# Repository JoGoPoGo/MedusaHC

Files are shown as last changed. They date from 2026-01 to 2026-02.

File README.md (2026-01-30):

# MedusaHC (Beta)

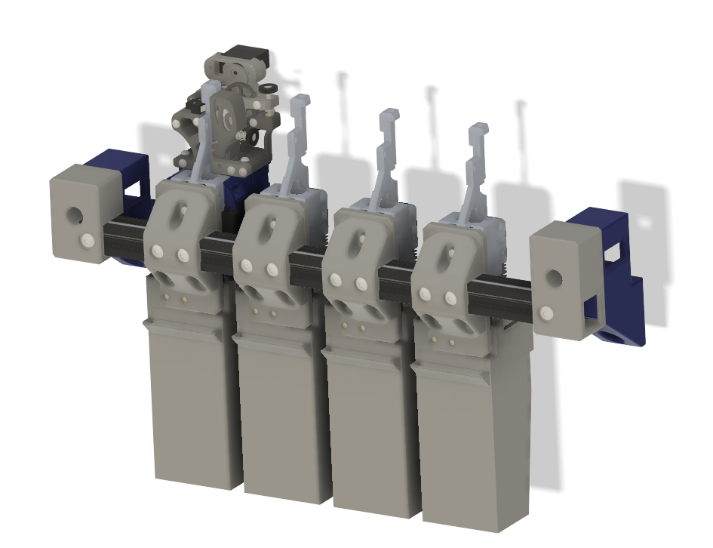
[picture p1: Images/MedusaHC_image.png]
MedusaHC


MedusaHC is an open-source toolchanger (hotend-changer) project.  
This is a beta version of the project. It is not finished yet, and there may be bugs during operation. The project will be updated gradually.

The project is fully open. You can do whatever you want with it.  
Only one request: it is not required, but I would be very grateful if you mention me in your modifications and derivatives of this project.

## Support the project

If you have the ability and desire to support the project, you can do it in several ways:

- Patreon — monthly support: https://patreon.com/Irbis3D  
- Ko-fi / Buy Me a Coffee — one-time donations: https://buymeacoffee.com/Irbis3D  
- YouTube Super Thanks — under any video: https://youtube.com/@Irbis3D  

Your support helps me create more content, upgrade gear, and keep experimenting with cool ideas.

Also, by buying parts using my links, you help as well.

## Credits

This project uses some work and ideas from the Dragonburner project by chirpy2605:  
https://github.com/chirpy2605/voron/tree/main/V0/Dragon_Burner

As well as from Sherpa_mini-Extruder by Annex-Engineering  
https://github.com/Annex-Engineering/Sherpa_Mini-Extruder

## Current status and compatibility

Right now, MedusaHC is an add-on for my Duender project:  
https://www.printables.com/model/1300968-duender-mgn9h-2x-creality-ender-3-corexy-convertio

Potentially, the project can be adapted for other classic CoreXY printers (as long as the printer has enough space in the front for the hotends and the bases). Theoretically, with small modifications, MedusaHC can also be adapted for CoreXY with a flying gantry.

The point of the project is that, unlike classic toolchangers, MedusaHC swaps only the hotend as a tool (with heater, thermistor, and fan). I am not the first who did this and I will not be the last. This topic is actively discussed and developed on my  
Discord server - https://discord.gg/ae44FHv786

## Documentation and audience

At the moment, the project does not have a full detailed assembly manual and is intended for experienced users.

Later I will make a full video where I explain how everything works and how to set it up. There is also a chance that, thanks to subscribers, after some time there will be a normal text manual with pictures.

For a general understanding, I recommend watching the first video about this project on my YouTube channel. You will not find all the information there, but you can get a general idea of how it works.

MedusaHC video (https://www.youtube.com/watch?v=hpV5Z1TnGdY)

## Parts, BOM, and files

Link to BOM

https://docs.google.com/spreadsheets/d/1xkOzb10DBJzalW4n1tYroh-m_ZFsTQipC1BpUh5ZMWY/edit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

For this project you need to buy quite a lot of parts. I tried not to use expensive and rare components. The list of all required parts can be found in the file MedusaHC_BOM.txt. This file will be updated as the project updates.

You can also find and export the print models yourself from the STEP file (the file was created in Fusion360. There were issues when opening it in FreeCAD, possibly due to some format mismatch).

There are also all STL files. In addition, you can use the 3MF file. This is an exported OrcaSlicer project, where you can see the orientation of all parts, the marked areas where supports are needed, and the settings I used to print the parts. This file will be useful later during setup, because it contains a full slicer config for MedusaHC.

To understand how everything should be assembled, for now use the STEP file. I printed all parts in ABS with 98% infill.

## Important notes

All parts must be printed with good enough quality so that parts do not get stuck inside each other. Some contact surfaces may need a bit of sanding to make them smooth.

When installing magnets (I glued them, and all magnet holes have access from the back for removing magnets), be careful and do not mix up the polarity.

The M3 pins that act as hotend guide pins must be pressed into the plastic as straight as possible. I hammered them in, but it is better to do it carefully using a vise. The two lower M3 30mm pins are mandatory. The upper M3 20mm pins are optional, if the hotend does not hold firmly enough.

On the hotend, the matching holes for the pins must be prepared. Personally, I used M3 inserts for this, and I drilled them first with a 3mm bit (they are usually about 2.9mm), and then with a 3.2mm bit (my bits are closer to 3.1mm). Even though the size looks odd, these drill bits are quite common.

Before drilling the actual part, I recommend testing on some test piece to make sure the hole is not too large. The pins must slide in freely, but must not be loose.

Maybe later it will be possible to use brass bushings of the correct diameter, but they take more space and may not fit.

The pressure lever spring for the feeder from the standard Sherpa Mini kit does not fit. I just found a suitable spring in my spare parts. When a spring with known dimensions is selected, I will add this information to the BOM.

The spring for the feeder opener lever is just a regular spring from a ballpoint pen.

Other than that, you just need to assemble everything carefully so nothing is loose and nothing binds. As I said earlier, I will explain more nuances in the video.

## Electronics

For this project, I use the **BTT Manta M8P** board. For a 4-hotend configuration, it can be considered the most optimal option. It has enough ports for absolutely everything, including 4 hotend heaters and even a dedicated Servo port (which is sufficient without a DC-DC converter). My configuration files are set up specifically for this board with a **CB2** module.  
https://s.click.aliexpress.com/e/_oktZaKt

Roughly the same capabilities are provided by boards like **BTT Octopus Pro**, **Kraken**, and other “large” boards, with the main difference being that the HOST is located separately.  
https://s.click.aliexpress.com/e/_c2wuASWJ  
https://s.click.aliexpress.com/e/_c3kPDyx1

When using other boards, it is possible to connect additional boards to a single host.

### Ports required per hotend (on the controller board)

For each hotend, the board must have the following ports:

- heater port (MOSFET-controlled; can be used either hotend heaters or the bed)  
- thermistor port  
- fan port (either PWM-controlled or a constant 24V port)  
- endstop port for the endstop located on the base of that hotend  

### Ports required for the toolhead

- one extruder motor port  
- part cooling fan port(s)  
- toolhead endstop port  
- port for the auto-calibration sensor (I use **BTT Eddy** connected via CAN)  
- servo port — if the board does not have a dedicated servo port capable of supplying stable 5V under load, it is recommended to power the servo via a **24V→5V DC-DC converter** from the main power supply  

### Power considerations

Additional hotends require additional power from the PSU.

From experience, a standard **350W** power supply is reliably sufficient for **2 hotends**.  
For **3 hotends**, it can be enough with a high-quality PSU.  
For **4 hotends**, it is definitely not enough.

In my setup with the **Manta M8P**, I use one **350W** power supply for the heated bed, and another **350W** power supply for everything else.

## Configuration setup

The main printer parameters, as before, are located in the `printer.cfg` file.  
In general, the configuration is no different from a standard Duender config.

The exception is that the extruder configuration block has been moved into the MedusaHC configuration file. More on this below.

### Additional modules

Personally, I use **klipper-tmc-autotune** for tuning motor drivers.  
(This is optional.)

### Display and sensors

In my opinion, the optimal screen is **BTT HDMI5**.

https://s.click.aliexpress.com/e/_c4odBUeJ

I also use the **Eddy-ng** module for auto-calibration and nozzle tap probing.  
In my setup, Eddy is connected via **CAN** (to save USB ports).

## Arcs support

The `[gcode_arcs]` block and the **Arc fitting** setting in the slicer allow the slicer to use **G2** and **G3** commands to print arcs instead of short straight segments.

On weak HOST systems, problems were observed with this feature. In such cases, it should either be disabled or the resolution should be set higher than **0.1**.

## System configuration files modified for this setup

### sensorless.cfg

This file has been modified quite heavily to make parking safer and to improve parking repeatability without endstops.

Parking is performed in the back-left corner (**X = min, Y = max**).  
First, the **Y axis** is parked (to avoid hitting hotends on the bases), then **X**, with small side movements. After that, **Y and X** are parked once again.

This ensures that the final parking always happens from the same distance relative to zero.

### line_purge.cfg

Modified so that the purge line is printed not along the X axis, but on the left side of the bed along the Y axis.

In my setup, **Adaptive** is disabled, so the line is always printed in the same place. It can be enabled if desired, in which case the line will be printed closer to the model.  
(Optional.)

### klipperScreen.conf

A menu with buttons for the main **MHC macros** has been added.  
(Optional.)

### macros.cfg

The `START_PRINT`, `END_PRINT`, `PAUSE`, and `RESUME` macros were heavily modified.

The start macro receives from the slicer the required temperatures for the hotends that will be used during the print and heats them up. At the moment, it does not take into account whether a hotend will be used soon or should wait its turn. I am not happy with this behavior yet, but I have not found a good solution so far.

The pause and resume macros are also heavily adapted for this system. The idea is that during tool changes, the printer remembers which tool it is trying to pick up. In case of a failure, the printer pauses and gives time to fix the issue.

It is enough to manually adjust the hotends so that they are in one of the “correct states” and then press resume. Regardless of what was done manually, the printer will automatically check which hotend it planned to take before the pause, park the X and Y axes (this is necessary if the motors skipped steps), and then ensure that the print continues with the correct hotend.

This procedure still has some shortcomings. A visible defect may remain on the model at that spot. Additionally, when parking with sensorless homing, the zero point may shift slightly, which can appear on the model as a small layer shift. In most cases, this shift is very small.

---

## MedusaHC configuration

The main files responsible for MedusaHC operation are:

- `MHC_config` — configuration of all hardware related to MHC  
- `MHC_variables` — variables for configuring various coordinates, speeds, and similar parameters  
- `MHC_macros` — the main file containing all macros responsible for MHC functionality  

And the `pin_watch.py` script — in the current version, a dedicated script is used to monitor sensor states. It listens to the sensors in real time and updates variable states accordingly. Based on this data, MHC determines what is installed where and checks for errors.

The file must be uploaded via FTP to the folder:

```

/home/biqu/klipper/klippy/extras

```

(` /home/pi/klipper/klippy/extras ` for Raspberry Pi users)

The script was integrated recently and has not been tested on different systems yet. If problems appear, I will make an additional version that works purely on macros, with manual state updates via a macro. (Feedback is required.)

All (or at least almost all) macros are designed to be universal and work with any number of hotends. The number of hotends is defined in the configuration and variables. My current config is for **4 hotends** (higher counts have not been tested yet).

## MHC setup

### MHC_config file

#### [pin_watch io] block

This block configures the `pin_watch` script.

- `sync_toolchanger: 1` — enables tool initialization in klipper-toolchanger (used for auto-calibration; explanation later).  
- `verbose` — enables additional console output with detailed pin state information.  
- `pin_e` — microswitch pin located on the toolhead.  
- `pin_t0`, `pin_t1`, etc. — microswitch pins on the bases of the corresponding hotends.

#### [duplicate_pin_override]

Since a single extruder motor is used for all tools, this block must specify the **step**, **dir**, and **enable** pins for that motor. This allows all extruders to use the same pins without causing configuration errors.

#### [extruder], [extruder1], etc.

Nothing special here. All extruders share the same **step**, **dir**, and **enable** pins. The rest is standard extruder configuration.  
A corresponding `extruder` block must be created for each hotend.

#### [gcode_macro T0], [gcode_macro T1], etc.

Mandatory macros that “create” additional tools in the system.  
The number of these macros must match the number of hotends.

#### [servo my_servo]

The last mandatory block. This defines the servo used to help open the feeder.

After that come optional parameters:

- fan configuration (if you are using controllable fan ports)  
- additional heater parameters  

It is recommended to change heater-related parameters only if there are heating problems, and only as a last resort, preferably temporarily.

---

### MHC_variables file

#### [save_variables]

This block defines the file where tool offsets are stored so they can be restored after a restart.  
(It is required when using auto-calibration.)

#### [gcode_macro TOOL_CFG]

This macro contains the main coordinates and distances used in the system, as well as the speeds and accelerations for the tool change procedure.

- `variable_x_t0`, `variable_x_t1`, etc. — the **X coordinate** where each hotend is mounted on its base.  
  In this configuration, the minimum safe distance between tools is **65 mm**. With small modifications, this distance could probably be reduced slightly, but not by much — maybe **5–10 mm**.

- `variable_y_safe` — the **Y coordinate** where the extruder with an inserted hotend can freely move left and right without hitting other hotends on their bases.  
  In my case, this coordinate is **negative**, because I used slightly extended profiles on the Y axis. This way, I do not lose any printable area. With standard profiles, there is a chance you will lose **5–10 mm** on the Y axis.

- `variable_y_latch` — the **Y coordinate** where the toolhead fully engages with the hotend.  
  This must be set very precisely so that the toolhead presses firmly against the hotend, but without causing the motors to skip steps.

- `variable_x_shift` — the distance the hotend needs to move along the X axis from `variable_x_t` in order to remove it from the base keyhole.

- `variable_fast_accel`  
- `variable_fast_speed` — speeds and accelerations for tool changes. During the change process, there are slowdowns that are calculated as proportions of these parameters.

- `variable_y_prime` — the **Y coordinate** where it is safe to prime filament into the bin.  
- `variable_y_brush` — the **Y coordinate** of the approximate center of the nozzle cleaning brush.  
- `variable_x_prime_shift` — the **X distance** from `variable_x_t` to the priming point.

#### [gcode_macro GLOBAL_STATE]

- `variable_max_tool: 4` — required by the macros to operate with the specified number of hotends.

- `variable_prime_amount` — the amount of filament (in mm) extruded during priming.  
  A small value (**7–8 mm**) is suitable when printing with a draft/wipe tower.  
  A larger value (**14–16 mm**) can be used for printing without a tower.

- `variable_prime_speed` — priming speed.

- `variable_prime_retract`, `variable_prime_retract_speed` — length and speed of the retract after priming.

- `variable_clean_move` — `1` to perform a clean move, `0` to skip it and just move to `y_safe`.

- `variable_clean_move_x`  
- `variable_clean_move_y`  
- `variable_clean_move_speed` — during cleaning, the hotend moves to the center of the brush and then performs a movement away from it using the parameters defined here.  
  Distances: a **positive** value moves in the positive direction, a **negative** value moves in the negative direction.

- `variable_clean_retract`  
- `variable_clean_retract_speed` — additional retract after cleaning.

Keep in mind that the lengths of these two retracts are linked to the slicer parameter **“Retraction when switching material”**.  
If the priming retract and the cleaning retract are **1 mm** each, then **“Retraction when switching material”** must be set to **2 mm**.

In some situations, with certain filaments and when printing without a draft tower, these parameters require additional calibration.

After this, there are parameters that are used internally by the macros.  
They should **not** be changed.

## Main macros file

And finally, the most important file. Nothing needs to be configured here (hopefully it will stay that way).  
I will not describe the system operation in full detail here. I will explain it a bit more in the video.  
Below is a short overview, just to understand the main algorithms.

---

### [delayed_gcode INIT_SENSOR_STATE]

This is a special G-code that runs on startup.  
It is responsible for:

- assigning variables that depend on printer parameters  
- initial tool assignment  
- applying tool offset values from the `saved_vars` file to the variables in `[gcode_macro TOOL_OFFSET]`

---

### Feeder control macros: OPEN, CLOSE and sub-macros

These macros control the feeder.

Running **two OPEN commands in a row is not allowed**, as this can cause the mechanism to jam.

There are no dedicated sensors to track the feeder state, so the state is stored in a variable. The printer uses this variable to determine whether the feeder is open or closed.

Since closing the feeder is relatively safe, it is forced on printer startup. From that moment on, the printer knows the feeder state and will not try to open it incorrectly.

#### Known issue

There is a known bug that I have not solved yet, related to opening the feeder.

If the printer received a motor disable command (`M84`) or if the motors were disabled by timeout, then on the **first feeder OPEN after that**, the extruder motor does not activate for some reason.

If the printer has been idle for a long time, or if you manually disabled the motors, then **before the next tool changes** you must execute the `OPEN` macro and then the `CLOSE` macro once.

After that, all further OPEN operations will work correctly.

I also added this procedure to the slicer start G-code, so this issue should definitely not occur during printing.

---

### Tool change macros: SET, DROP and sub-macros

Next come the `SET` and `DROP` macros and their sub-macros.

Splitting procedures into multiple macros is required, because within a single macro the firmware does not see variable updates. I will explain this in more detail in the video.

In general terms:

The **main macro responsible for all tool change procedures is `SET`**. This is the macro called by the `T` macros.

When `SET` is called with a tool parameter (`SET T=0`, `SET T=1`, etc.), the printer checks what is currently installed, based on data from the `pin_watch` script object.

- If no hotend is installed, the printer will pick up the requested hotend.  
- If a different hotend is installed, the printer will first drop it, then pick up the requested one.  
- If the requested hotend is already installed, the printer will simply apply the offsets for the selected tool and finish.

All of this happens automatically, without the need to manually specify anything.

Thanks to the `pin_watch` script, the printer always knows its state, even if you manually remove or install hotends.

---

### DROP macro and error handling

The `DROP` macro can be used independently from `SET` to drop the currently installed hotend.  
However, for manual dropping it is better to use the dedicated `DROP_CLOSE` macro.

All pickup and drop macros include checks.

If after dropping or picking up a hotend the script detects that the sensor state does not match the expected one (for example, the drop failed, pickup failed, or some other hotend fell off its base), the printer will pause and enter an error state.

After fixing the problem and resuming, the printer will pick up the planned tool and continue printing.

As mentioned earlier, this logic works, but still requires further optimization.

---

## Orca Slicer configuration

All slicer settings can be viewed by opening the file `4Rca cube.3mf` as a project.

All MHC-specific parameters are located in the printer settings.

### Machine G-code tab

The following sections are modified:

- Start G-code  
- End G-code  
- Change filament G-code  

The **Layer change G-code** also includes a modification that assigns a layer variable. It is not used at the moment, but may be useful in the future.

### Multimaterial tab

You must specify the number of extruders. After that, separate tabs with settings for each hotend will appear.

All print parameters related to multimaterial printing are also located in the **Multimaterial** tab.

---

## G-code post-processing script

In addition, to optimize the workflow, I use a G-code post-processing script called `SET_FINISH.py`.

This script slightly changes the order of movements when transitioning back to printing after a tool change.  
It also replaces some temperature commands that include waiting with non-waiting commands.

This is done so that, when **Ooze prevention** is enabled, the printer does not wait for temperature stabilization after every tool change.

Be careful with **Ooze prevention** settings. The heating time must always be sufficient for the hotend to reach the target temperature.

To use this script, **Python must be installed on the computer**.  
You must specify the path to Python and to the script itself in the **Others** tab, in the **Post-processing Scripts** section.

In my case, this block looks like this:

```

"C:\Users\their\AppData\Local\Python\pythoncore-3.14-64\python.exe" "C:\Firmware\Medusa HC Beta CONFIG\SET_FINISH.py" 12
;

```

## Tool offset calibration

Offsets work relative to the first tool.  
That means all offsets for **T0** are equal to `0`, and all other tools are calculated relative to **T0**.

Keep in mind that this system uses **G-code offsets**.  
That is, how much the entire coordinate system needs to be shifted so that the hotend ends up in the same position as **T0**.

Do not confuse this with *tool offset*, where the value indicates how much the hotend itself is shifted from the desired point.

As a result, **tool offset has the opposite sign of the G-code offset**.

---

### Manual tool offset calibration

In the `MHC_macros` file, inside the `INIT_SENSOR_STATE` macro, you need to comment out  
(add `#` at the beginning of each line) the entire **“Initial tool offset setup”** block.

---

### Z offset calibration

Z calibration is done manually, via the web interface or the printer menu.

Lower each hotend to the bed and calculate the offset relative to the first hotend.

---

### XY offset calibration

For this, you need to print special calibration models.  
I used this one:

https://www.printables.com/model/129617-offset-xy-dual-extruder-idex-calibration

Place **one fewer copy** of this model than the number of hotends on the bed.

- The bottom part of all copies is printed with **T0**
- The top parts are printed with different hotends: **T1, T2**, and so on

Keep in mind that this test shows **tool offset**, so for MHC you need to **invert the sign** of the obtained values.

The resulting offsets must be written into the corresponding variables in the  
`MHC_variables` file, inside the `TOOL_OFFSET` macro.

---

## Automatic Z offset calibration using Eddy-ng

Basic Eddy-ng installation is done according to the standard instructions.

The Eddy mount in this project is made without adjustment and fits the Bambulab hotend clones that I use.

Eddy is quite sensitive to installation height, so you may need to slightly shift the holes in the model and reprint the mount.

The standard Eddy-ng feature set does **not** support working with multiple tools.

For auto-calibration to work, you must replace the `probe_eddy_ng.py` script located in:

```

/home/biqu/eddy-ng

```

with the modified `probe_eddy_ng.py` from this project.

This version can pass the required data to calculate offsets for all tools.

To enable auto-calibration, you need to include the file `eddy_ng_features.cfg`.  
It contains all the required macros.

Automatic calibration of all available tools can be started with the macro:

```

TOOL_Z_CALIBRATION

```

For accurate calibration, make sure the nozzles of all tools are clean.

After auto-calibration, the calculated offsets are saved to the `saved_vars` file and will be applied on every printer startup.

---

## Full auto-calibration using Sexball

Theoretically, I have an almost working script for auto-calibration using the Sexball sensor.  
However, I am not satisfied with how the values are calculated.

Because of this, I added the ability to partially integrate the **klipper-toolchanger** plugin by Viesturs Zariņš into MHC:

https://github.com/viesturz/klipper-toolchanger

The plugin is installed using the command from its manual:

```

wget -O - [https://raw.githubusercontent.com/viesturz/klipper-toolchanger/main/install.sh](https://raw.githubusercontent.com/viesturz/klipper-toolchanger/main/install.sh) | bash

```

Configuration settings for klipper-toolchanger are located in `toolchanger.cfg`.

The configuration is minimal:

- a `[toolchanger]` block with everything disabled  
- one `[tool T0]`, `[tool T1]`, etc. block for each hotend  

In practice, klipper-toolchanger does almost nothing.  
All MHC functionality still works exactly as before.

The only thing klipper-toolchanger needs for auto-calibration is to know which tool is currently active and to pass calibration data back.

To synchronize MHC state with it, you must set:

```

sync_toolchanger: 1

```

in the `[pin_watch io]` script configuration.

To receive calibration data, you must place the modified `tools_calibrate.py` script into:

```

/home/biqu/klipper-toolchanger/klipper/extras

```

Since we are modifying an internal script, automatic updates of klipper-toolchanger will show an error.

Because of this, at this stage I do **not** recommend enabling auto-update for klipper-toolchanger in `moonraker.conf`.

If this approach remains the same, a separate fork with updates will be required.

---

## Auto-calibration settings

The base auto-calibration settings have not changed.  
They are located in `calibrate-offsets.cfg`, in the `[tools_calibrate]` block.

In the `CALIBRATE_MOVE_OVER_PROBE` macro, you must specify an approximate point above the center of the Sexball sphere.

The standard macros from klipper-toolchanger are not suitable.  
A modified `calibrate-offsets.cfg` is also included in this project.

For fully automatic calibration with saving and applying all offsets, run the macro:

```

CALIBRATE_AND_SAVE_OFFSETS

```

---

## Final notes

This project is fully open source. You are free to use it, modify it, and build your own derivatives.

If you find the project useful, any kind of support helps — it allows me to spend more time on development, testing, and experiments. The project will be updated gradually, as new ideas appear and as I have the time and resources to work on it.

Most discussions about this project and similar toolchanger concepts take place on my  
Discord server:

https://discord.gg/ae44FHv786

That is where new ideas are tested, problems are discussed, and future directions are shaped.

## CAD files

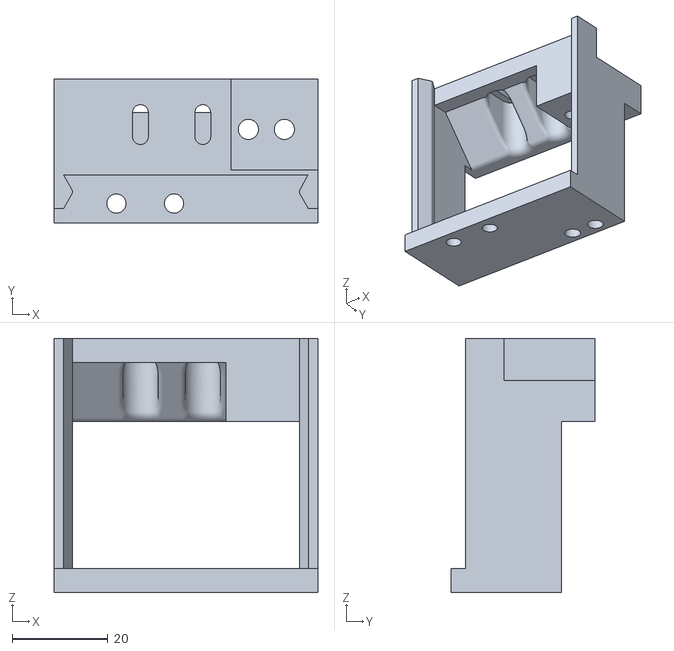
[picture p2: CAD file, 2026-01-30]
STLs/Base/Base_Bin_Main.stl
55.0 x 30.0 x 53.0

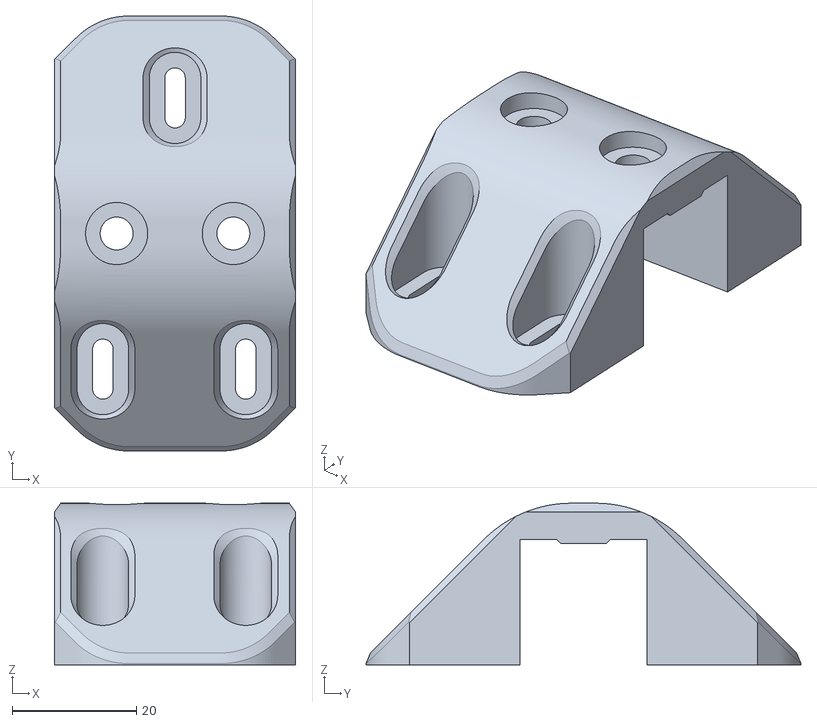
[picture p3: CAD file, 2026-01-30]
STLs/Base/Base_Mount_Main.stl
38.8 x 70.0 x 26.0

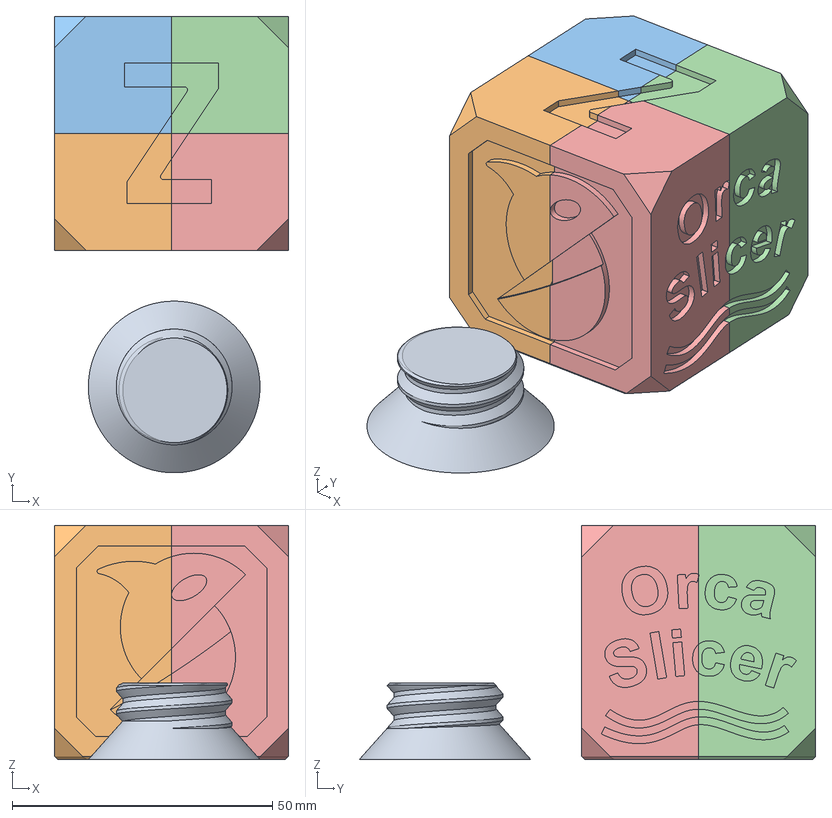
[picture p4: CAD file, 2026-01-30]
3MF/4Rca cube.3mf
45.0 x 87.8 x 45.0 mm
OrcaPlug
OrcaCube x 4

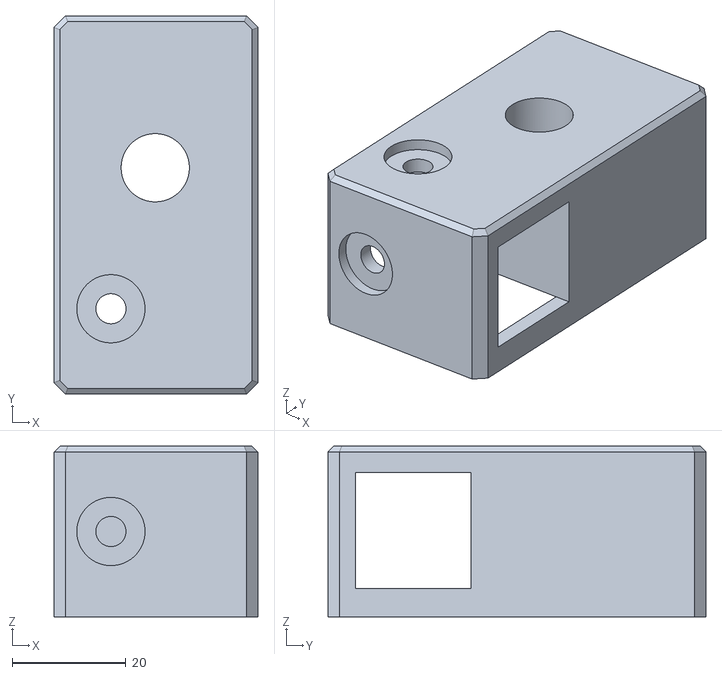
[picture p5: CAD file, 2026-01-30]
STLs/Base/Base_Profile_Mount_R.stl
35.9 x 66.5 x 30.0

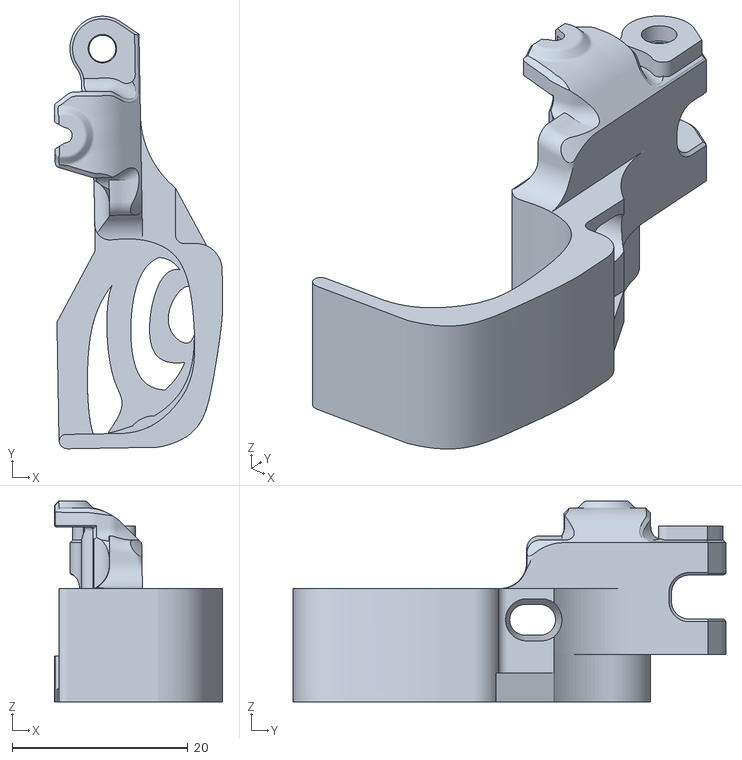
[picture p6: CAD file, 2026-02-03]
STLs/Feeder/Feeder Lever Mail v1.stl
19.2 x 49.3 x 22.9

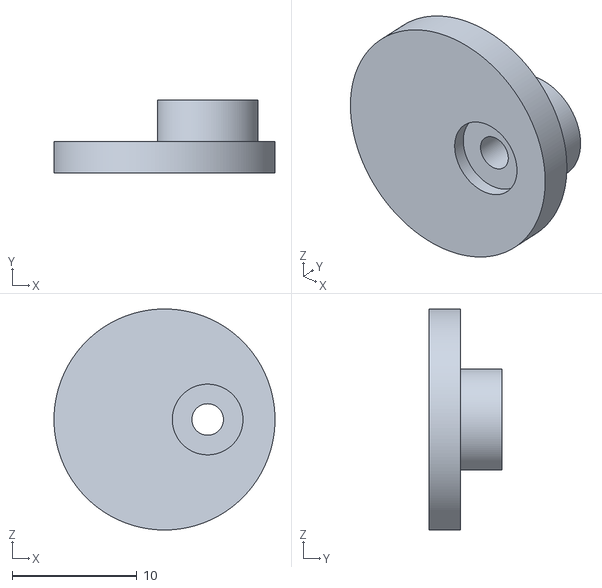
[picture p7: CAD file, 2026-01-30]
STLs/Toolhead/MG90S Opener v1.stl
17.7 x 5.86 x 17.7

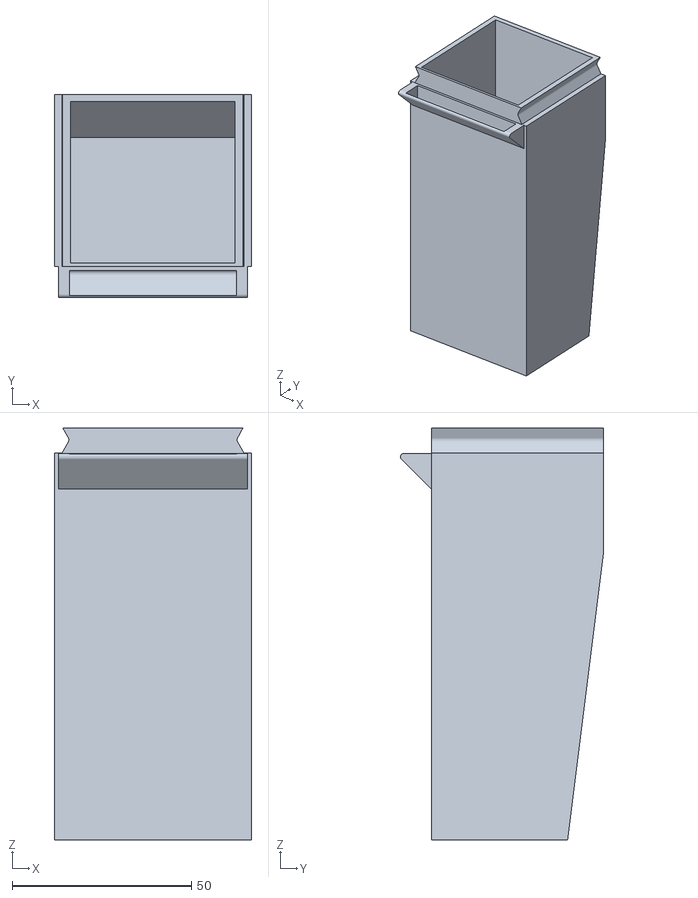
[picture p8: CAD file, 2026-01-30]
STLs/Base/Base_Bin.stl
55.0 x 56.6 x 114.8

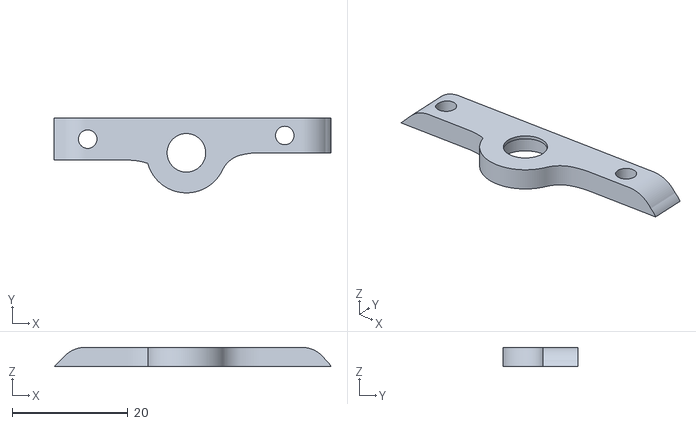
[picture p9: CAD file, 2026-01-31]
STLs/Feeder/Feeder Lever Cover.stl
47.9 x 12.9 x 3.35

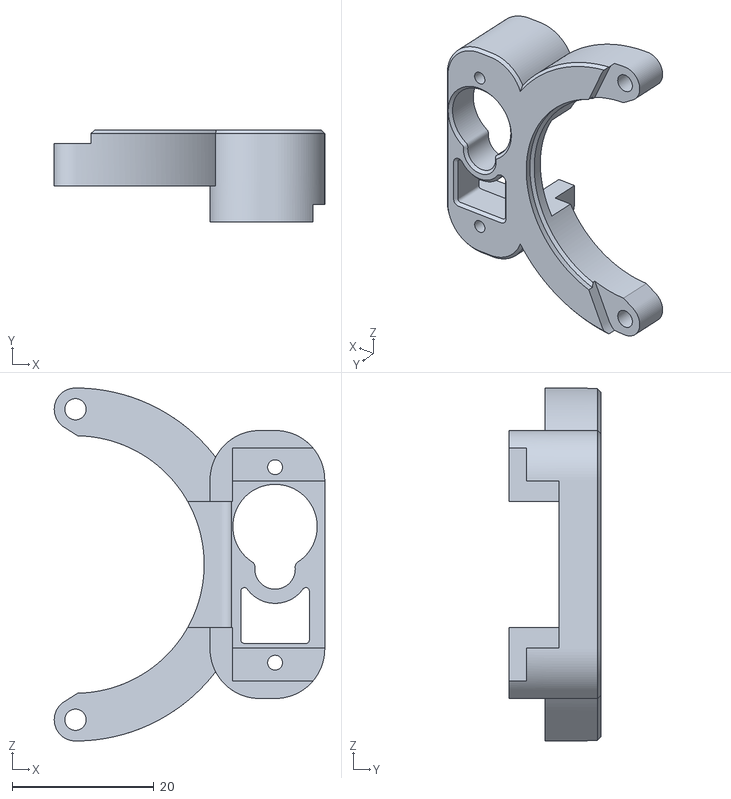
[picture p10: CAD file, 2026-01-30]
STLs/Toolhead/Servo_Mount.stl
38.2 x 13.0 x 49.8

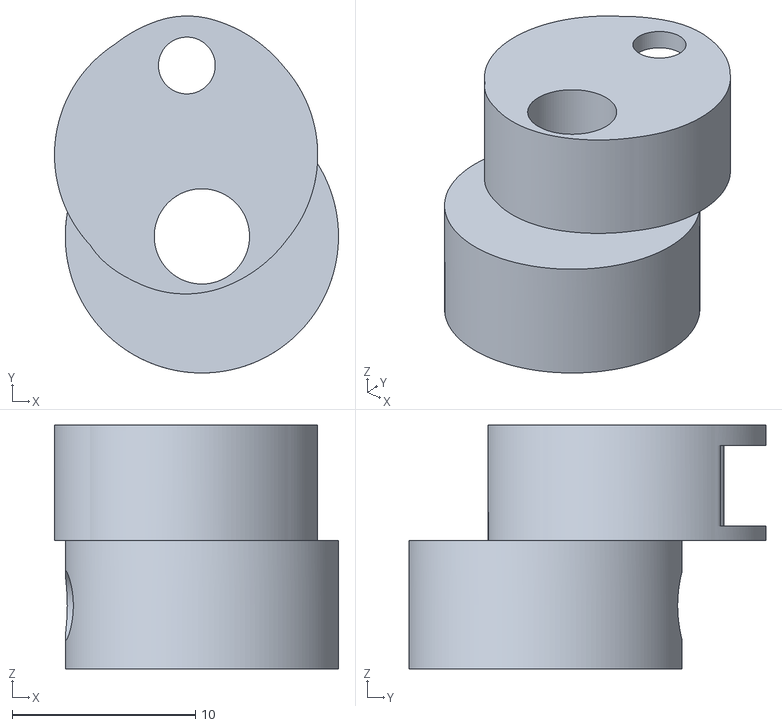
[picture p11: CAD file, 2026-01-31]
STLs/Feeder/Feeder Opener.stl
15.5 x 19.5 x 13.3

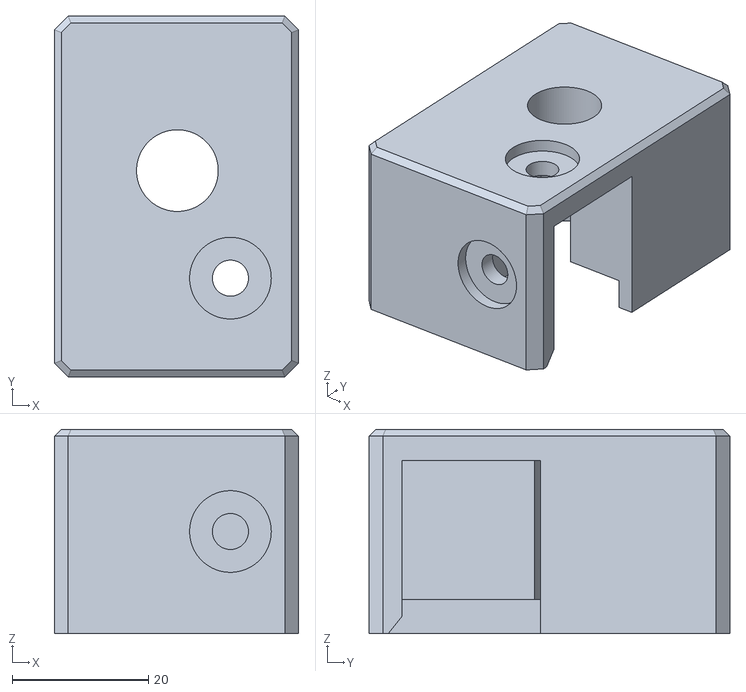
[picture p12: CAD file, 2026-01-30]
STLs/Base/Base_Profile_Mount_L.stl
35.9 x 53.0 x 30.0

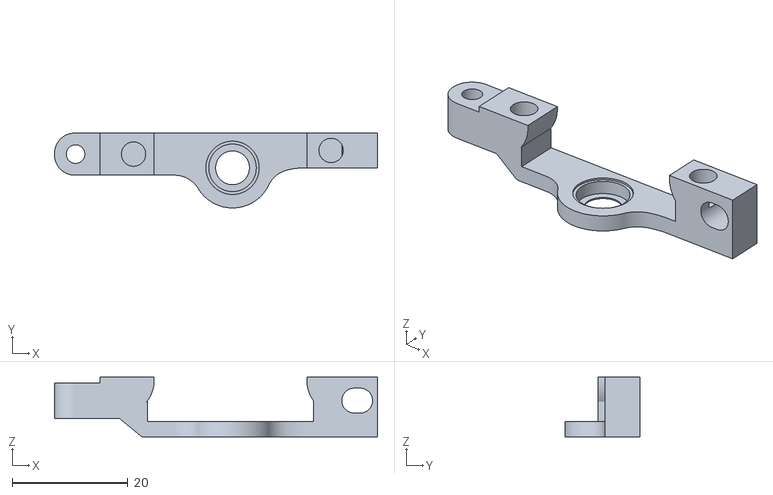
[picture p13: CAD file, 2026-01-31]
STLs/Feeder/Feeder Lever.stl
55.7 x 12.9 x 10.3

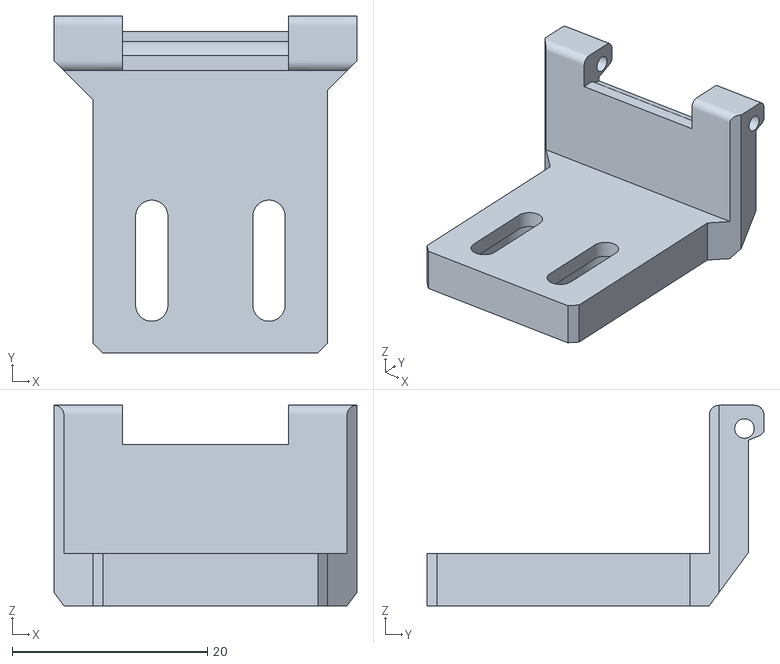
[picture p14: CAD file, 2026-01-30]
STLs/Base/Brush_Mount.stl
31.0 x 34.5 x 20.5

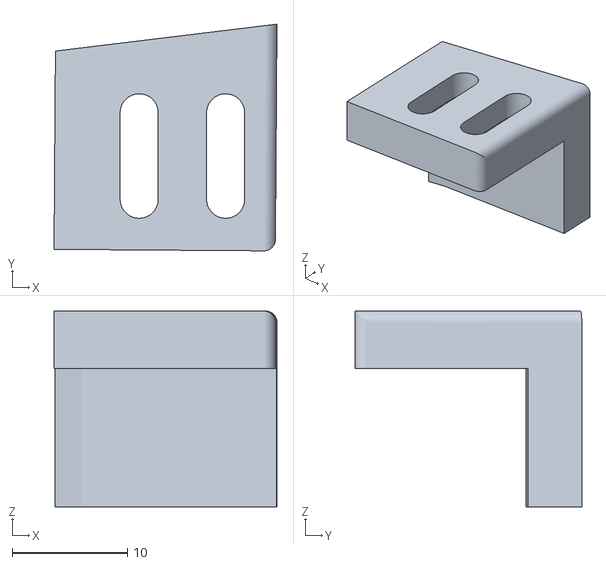
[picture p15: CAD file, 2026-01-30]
STLs/Base/Nozzle_Close.stl
19.3 x 19.7 x 17.0

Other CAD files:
STLs/Base/Base_Mount_Plate.stl

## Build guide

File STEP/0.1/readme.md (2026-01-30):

Link to full STEP file

https://drive.google.com/file/d/1BfwxK7Hq4RHmAjxl-eghoNYVGK8Xf2VU/view?usp=sharing

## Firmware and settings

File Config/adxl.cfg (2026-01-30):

[mcu adxl]

serial: /dev/serial/by-id/usb-Klipper_rp2040_E6647C740355A936-if00


[adxl345]
cs_pin: adxl:gpio9
spi_software_sclk_pin: adxl:gpio10
spi_software_mosi_pin: adxl:gpio11
spi_software_miso_pin: adxl:gpio12

[resonance_tester]
accel_chip: adxl345
probe_points:
    115, 115, 50

#[adxl345]
#cs_pin: PC10
#spi_bus: spi2
#spi_speed: 1000000
#rate: 3200

#[adxl345]
#cs_pin: PD6
#spi_software_sclk_pin: PB6
#spi_software_mosi_pin: PB5
#spi_software_miso_pin: PB7
#spi_speed: 500000
#rate: 3200

#[samd_sercom accel_spi]
#sercom: sercom7
#tx_pin: duet:PC12     # MOSI (SPI2_MOSI)
#rx_pin: duet:PC15     # MISO (SPI2_MISO)
#clk_pin: duet:PC13    # SCK  (SPI2_SCK)

#[static_digital_output hold_other_cs]
#pins: duet:PC7        # держим второй CS (CS1) в 1

#[adxl345]
#cs_pin: duet:PC7      # SPI2_CS1 (именно его ты подключил)
#spi_bus: sercom7
#spi_speed: 500000
#rate: 3200

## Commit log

2026-01-30 Create hotend
2026-01-30 Create toolhead
2026-01-30 Rename Снимок экрана 2026-01-27 090948.png to MedusaHC_image.png
2026-01-31 Rename Feeder Lever Mail v1.stl to Feeder Lever Main.stl
    [Feeder Lever Main.stl]
2026-01-31 Update and rename Feeder Opener (1).stl to Feeder Opener.stl
    [Feeder Opener.stl]
2026-01-31 Update and rename Feeder Lever 2 Cover.stl to Feeder Lever Cover.stl
    [Feeder Lever Cover.stl]
